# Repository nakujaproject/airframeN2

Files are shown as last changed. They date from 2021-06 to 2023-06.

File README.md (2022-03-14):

# AirframeN2

This is the repository for airframe sub-group relating to N1 rocket.






## Oboarding

For new member please checkout out onboard document [here](Onboarding/newEmployee.md)

## Research

For visitors checkout our research done by members of the airframe team [here](Research/)

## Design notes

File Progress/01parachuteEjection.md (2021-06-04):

# Parachute Ejection

This is how we will eject our parachute so that we can be able to recover our rocket after launch. There are many ways to recover the rocket mainly subdivided into pyrotechniques and non-pyrotechniques. I decided to use non-pyrotechniques as it is mainly fault tolerant and easier to make.

One mechanism in **DetMech** which was developed to automatically detach a rocket from its parachute line based on the apogee of the rocket. It is designed to assist in recovering rockets stagged by their parachutes. This method utilizes the use of a servo motor to open and close the hatch in order to eject the parachute.

Other mechanisms include :

1. Using a rubber band. The rubber band is wrapped around the body, nosecone or parachute door holding it in place until it is released.
2. Solenoid. The solenoid is used to activate thee recovery system via on board electronics usually in form of a pulse or a discharge from a capacitor. The solenoid activates a pin similary to the servo motor.
3. Mechanical armature. This involves using mechanical levers, strings and the likes.
4. Pyrotechnic. This is using a pyrotechnic charge whihc is ignited, or a wire is heated to activate the recovery system

One of the best methods is using mechanical systems since their failure rate is low. I chose servo motor as it averagely performs better in terms of cost and mode of design. The servo is an electromechanical system thus utilizing both the mechanical and electrical aspects.

## How it works

Ther mechanism is based on a simple clamp that holds the latch on to the nose cone. At the appropriate time, after maximum height has been reached with a specified delay, the clamp is moved which releases the parachute. By attaching the latch, nose cone and payload chamber to the parachute you will have a better chances in recovering the whole rocket.

The clamp is made up of a micro servo arm which is made of plastics. The latch on the other hand is made up of tough PLA material used in 3D printing the whole rocket. There can be large lateral force on the clamp during parachute opening. Aerodynamically, it has a low profile.

The bottom plate, payload chamber, which houses the electronics, is attached to the nose cone with screws rather than being glued due to large forces involved. The main parachute line should be fitted with a shock cord to reduce the stress on the clamp.

There is a little groove is to prevent the latch from moving side to side. This mechanism is contolled by the flight computer. This gives the rocket crew a chance t retrieve the rocket easily.

## More info

Using a micro servo to eject the parachute as well as detach it, will save on weight and complexity. The dual purpose mode of a single servo would be based on Christian Thomsen's RC dual chute release mechanism.
The servo could be controlled externally by a remote control. Allowing the rocketeer to release the rocket when appropriate.
A variation on the mechanism could make it completely internal to the rocket body reducing drag.
Another alternative is to replace the servo motor with a water soluble paper or plastic (such as Polyvinyl alcohol). This could be wound around the clamp to hold it down, and when it rains or humidity in the air would cause it to dissolve and release the mechanism.

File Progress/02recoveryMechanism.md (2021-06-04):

# Recovery mechanism

This is the actual deployment of the recovery mechanism in slowing down the rocket. This also includes opening latches to push out parachutes.

Some examples of the recovery mechanisms are:

1. Parachutes. This is the most effective method of recovery system.
2. Side deployment. The parachute is ejected on the outside of the rocket using some kind of spring mechanism
3. Inline deployment. The parachute is ejected along the axis of the rocket.
4. Streamer. It is deployment same as the parachute.
5. Wings, glider. This is commonly ised as passive control.
6. Changing CG, This involves changing the weight of the rocket in order to shift stability.
7. Changing CP, centre of pressure in order to move air surfaces to change the flight's stability.
8. Balloon. A balloon can be inflated from an internally stored pressure chamber in order to increase the rocket's drag.

For N1 rocket we choose the parachute system. This is too slow the rocket to an acceptable descent rate to ensure survival of the avionics. There is usually a backup system e.g deploying to parachutes or using two different methods.

A parachutre is basically a flexible device whose function is to produce drag. It slows down the rocket to a decent speed.

Dual deploy means there is a primary and secondary parachute to reduce the impact. The first is generally stronger to overcome large velocities and stabilize the rocket. The second one is attached to teh first one via a tow-line and is used to reduce drift away from launch site.

Shock cord, rubber band, is used to as a gravity coupler. This is to store kinetic energy before opening up the parachute.

Main canopy is attached to the towline to provide soft landing

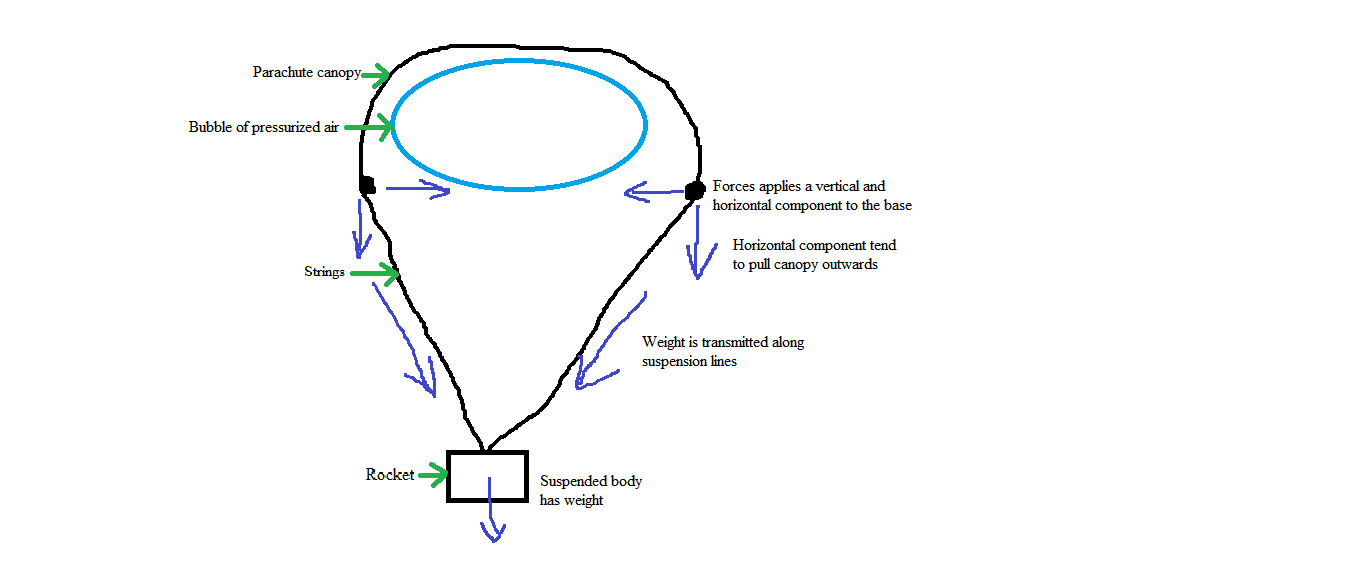
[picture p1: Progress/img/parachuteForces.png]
Parachute Forces


From the diagram above we can clearly see, according to Newton, the addition of more drag (an adverse force) results in a lower acceleration.

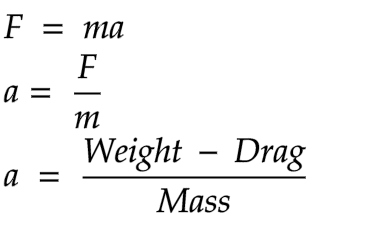
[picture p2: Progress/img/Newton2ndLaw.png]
Newton Second Law


Whether the body decelerates (negative acceleration) or not depends on the velocity and altitude of the parachute deployed.

If the body has high velocity at parachute ejection, the drag may be greater than weight.  In this case the body will decelerate. If the body has low velocity at parachute ejection, the drag may be lower than weight.  In this case the body will accelerate.

Velocity changes so as the drag. At equilibrium point the drag is equal to the weight.

If drag starts off lower than weight, acceleration will be positive. This increases velocity and drag. Drag will eventually equal weight and acceleration become zero.

When velocity isn't changing it has reached terminal velocity and it will descend at a constant velocity.

For terminal velocity drag = weight.

The parachute design process needs:

- desired shape
- weight
- drag coefficient
- determine impact velocity
- canopy area

### Desired shape

We will look at three main designs:

1. Cross

    - Easy to build

    - Lower coefficient of drag, (0.70)

    - More stable

2. Square

    - Easiest to build

    - Moderate coefficient of drag, 0.73

    - Less stable

3. Circular

    - Difficult to build

    - Higher coefficient of drag, 0.78

    - The Least stable

### Weight

At terminal velocity, drag should be equal to weight, 9.8067 N

### Drag coefficient

The drag coefficient itself depends on the Reynolds number Re. For small enough Reynolds number (of the order of few thousands or smaller) the dependence is mild and the drag coefficient is approximately constant.

### Determine impact velocity

### Canopy area

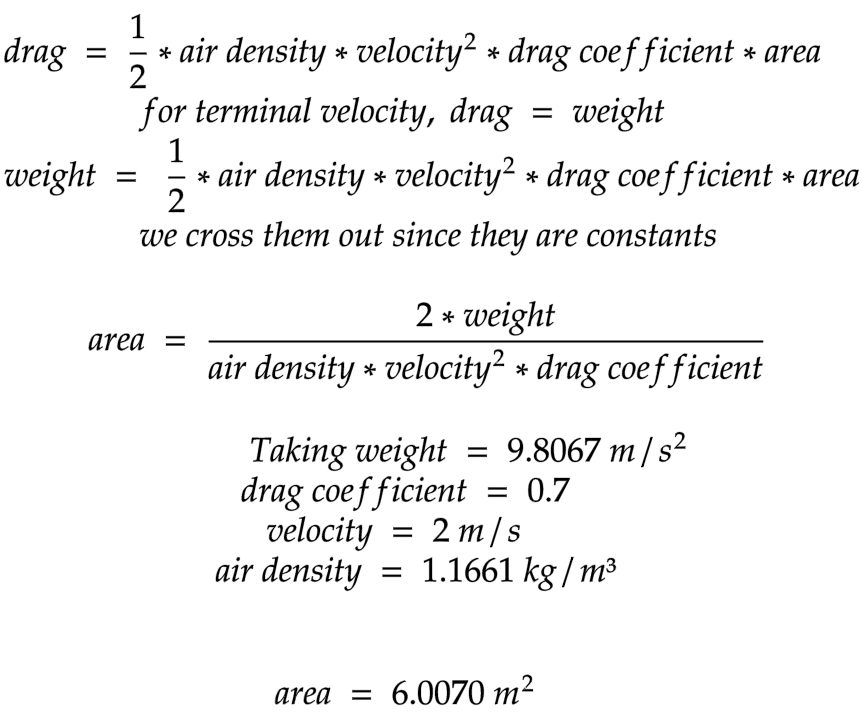
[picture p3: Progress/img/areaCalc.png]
Area calculation


Hints:

1. Get atmospheric temperature of where I am testing, [Juja](https://www.accuweather.com/en/ke/juja/828638/hourly-weather-forecast/828638)
2. Calculate the air density of where you are testing, [Juja](https://www.omnicalculator.com/physics/air-density?c=KES&v=P:1013!hPa,Temp:28!C,aaa:1.000000000000000,T:11!C)
3. Check if our area provides the drag equal to weight, [here](https://www.omnicalculator.com/physics?c=USD&v=Cd:0.7,u:2!ms,rho:1.1661!kgm3,A:6.00702!m2)

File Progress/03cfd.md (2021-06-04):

# CFD

Computational fluid dynamics (CFD) is a branch of fluid mechanics that uses numerical analysis and data structures to analyze and solve problems that involve fluid flows.

## Methodology

Some basic procedures during preprocessing are:

- The geometry and physical bounds of the problem are defined using computer aided design (CAD). From there, data is processed and the fluid volume is extracted.
- The volume occupied by the fluid is divided into discrete cells. The volume may be uniform or non-uniform or structured or unstructured.
- Physical modeling is defined, the equations of fluid motion + enthalpy + radiation + species conservation.
- Boundary conditions are defined. This involves specifying the fluid behaviour and properties at all bounding surfaces of the fluid domain. For transient problems, the initial conditions are also defined.
- The simulation is started and the equations are solved iteratively as a steady-state or transient.
- Finally, a postprocessor is used for the analysis and visualization of the resulting solution.

### Definitions

The term **compressible** refers to the relationship between density and pressure. If a flow is compressible, changes in fluid pressure affect its density and vice versa. For compressible flow, particularly supersonic flows, downstream pressure cannot affect anything upstream and the pressure equation is hyperbolic, requiring only upstream boundary conditions.

**Laminar flow** is characterized by smooth, steady fluid motion.

**Turbulent flow** is fluctuating and agitated motion. The measure of whether a flow is laminar or turbulent is the speed of the fluid. Laminar flow is typically much slower than turbulent flow. The dimensionless number which is used to classify a flow as either laminar or turbulent is the Reynolds number defined as:

Reynolds number

Where **rho** is the density, **V** is the velocity and **meu** is the viscosity. For Reynolds numbers greater than ~2500, the flow exhibits turbulent flow phenomena. Most engineering flows are turbulent.

The three-dimensional time-dependent continuity, Navier-Stokes and energy equations apply to laminar as well as turbulent flow. However, due to the infinite number of time and length scales inherent in turbulent flows, the solution of these equations require a huge number of finite elements even for a simple geometry as well as nearly infinitesimally small-time-steps. For most practical applications, it is unreasonable to model the flow in this manner.

To circumvent the need for such immense computer resources, the governing pdes are averaged over the scales present. There are several choices of scale types available for averaging. Autodesk Simulation CFD solves the time-averaged governing equations.

The time-averaged equations are obtained by assuming that the dependent variables can be represented as a superposition of a mean value and a fluctuating value, where the fluctuation is about the mean. For example, the x-velocity component can be written as:

Flactuation value

Where **U** is the mean velocity and **u'** is the fluctuation about that mean. This representation is substituted into the governing equations and the equations themselves are averaged over time.

#### Continuity Equation

Continuity Equation

**Wind tunnels** are large tubes with air blowing through them which are used to replicate the interaction between air and an object flying through the air or moving along the ground. Researchers use wind tunnels to learn more about how an aircraft will fly. The wind tunnel moves air around an object, making it seem as if the object is flying.

### Pressure measurements

Pressure across the surfaces of the model can be measured if the model includes pressure taps. This can be useful for pressure-dominated phenomena, but this only accounts for normal forces on the body.

### Flow visualizations

Because air is transparent it is difficult to directly observe the air movement itself. Instead, multiple methods of both quantitative and qualitative flow visualization methods have been developed for testing in a wind tunnel.

### Physics of fluid

Fluid is liquid and gas. For example, water and air. Fluid has many important properties, such as velocity, pressure, temperature, density and viscosity.
The density (1) of a fluid is its mass per unit volume. If the density of fluid is constant (or the change is very small), we call the fluid is incompressible fluid. If the density of fluid is not constant, we call the fluid is compressible fluid. Normally, we can treat water and air as incompressible fluid. If the fluid is incompressible, we can simplify the equations for this type of fluid.

Density

The viscosity (2) is an internal property of a fluid that offers resistance to flow. For example, to stir water is much easier than to stir honey because the viscosity of water is much smaller than honey

Viscosity

## The Process

### First open up Fusion 360

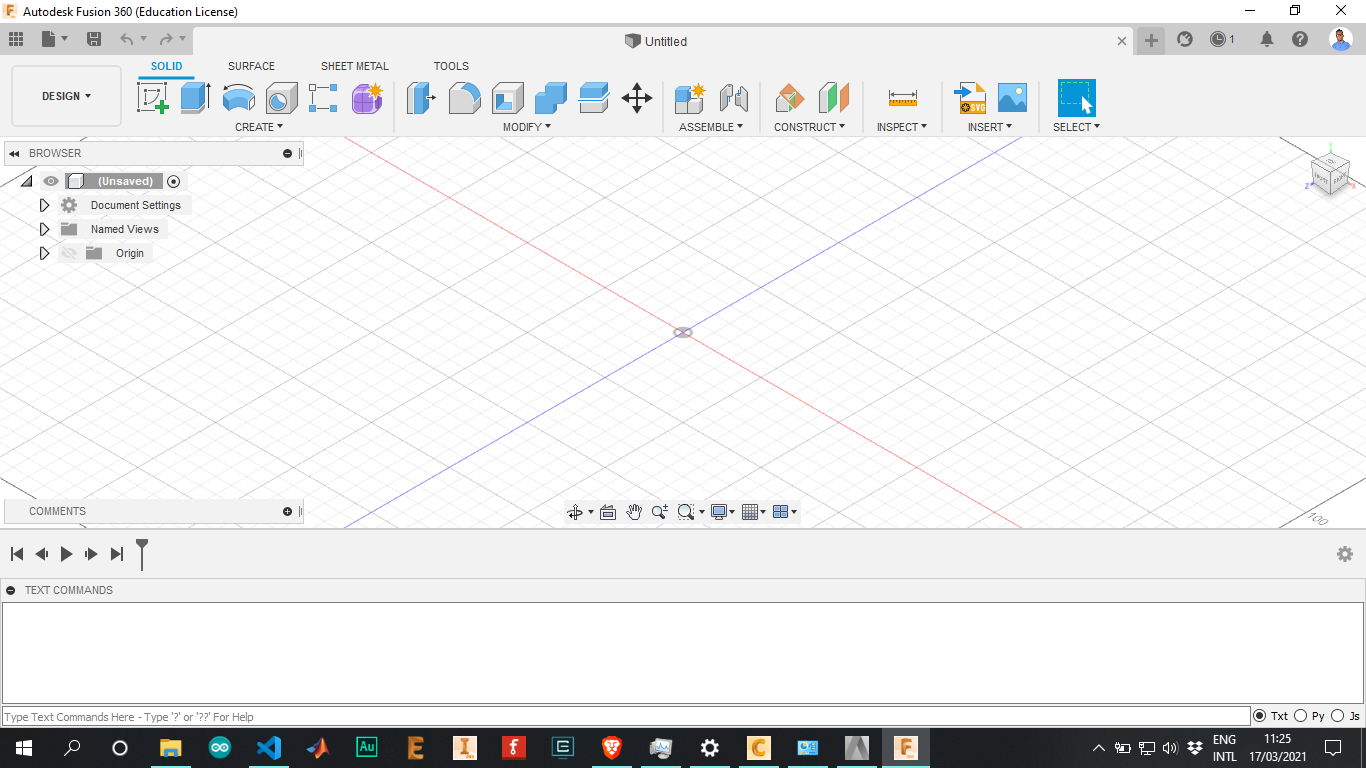
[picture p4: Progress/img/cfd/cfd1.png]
[](img/cfd/cfd1.png)

Load the assembly model

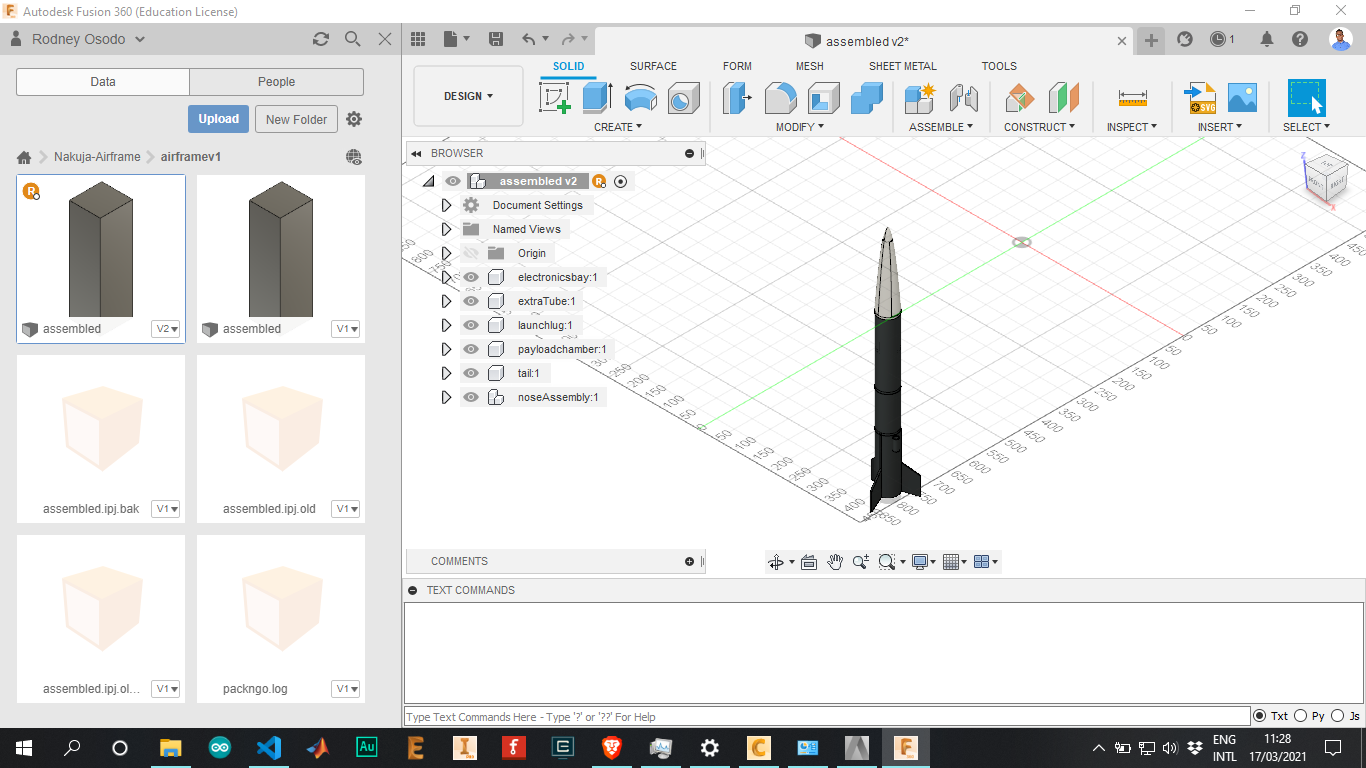
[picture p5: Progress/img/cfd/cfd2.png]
[](img/cfd/cfd2.png)

Create a wind tunnel around the model 

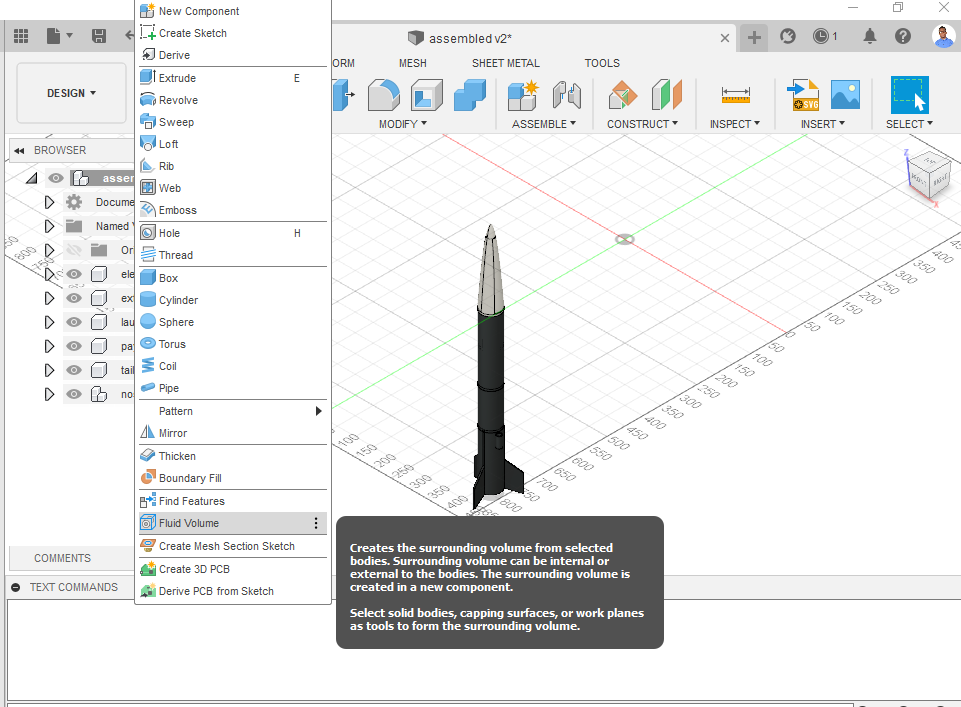
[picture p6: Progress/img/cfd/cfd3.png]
[](img/cfd/cfd3.png)

Pad the model with spacing of your choice, 50mm all around

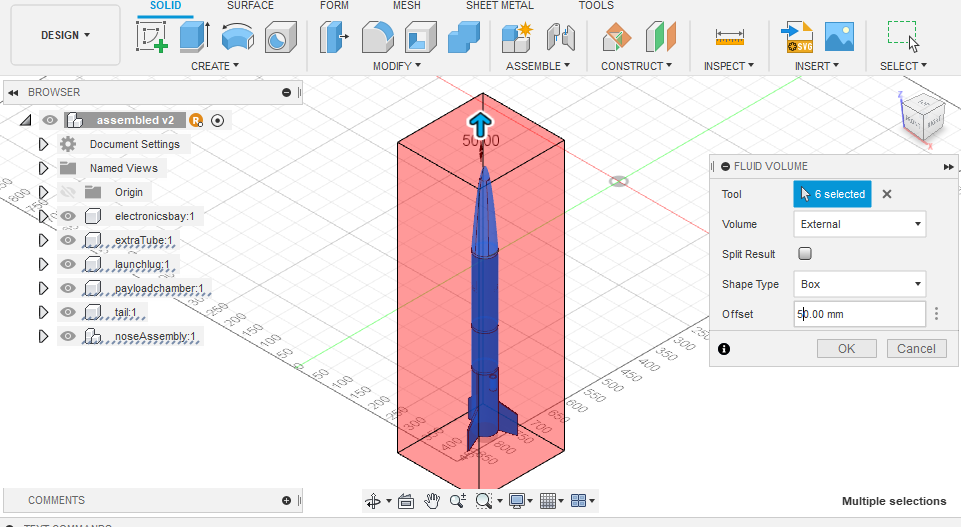
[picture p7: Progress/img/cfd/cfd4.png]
[](img/cfd/cfd4.png)

The wind tunnel is now created

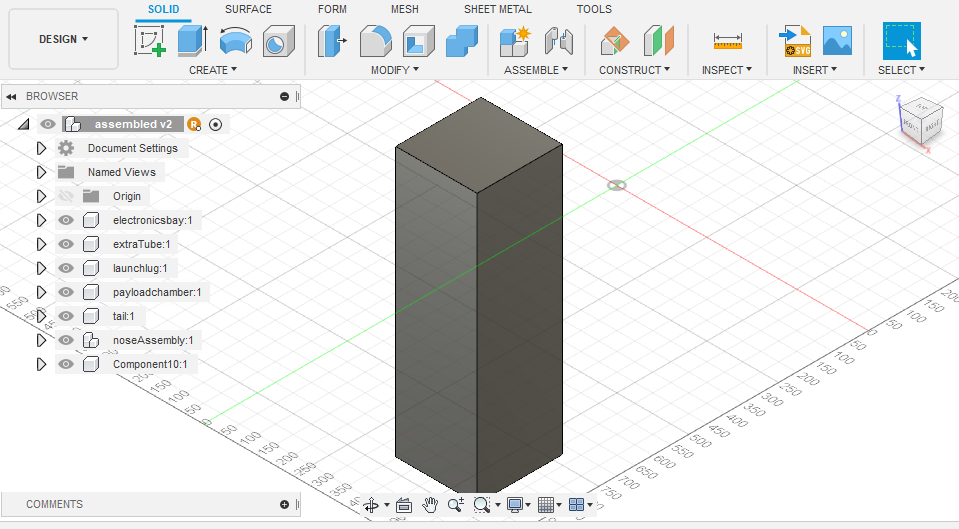
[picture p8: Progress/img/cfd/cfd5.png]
[](img/cfd/cfd5.png)

Export the file as `.step` or `.stp` file

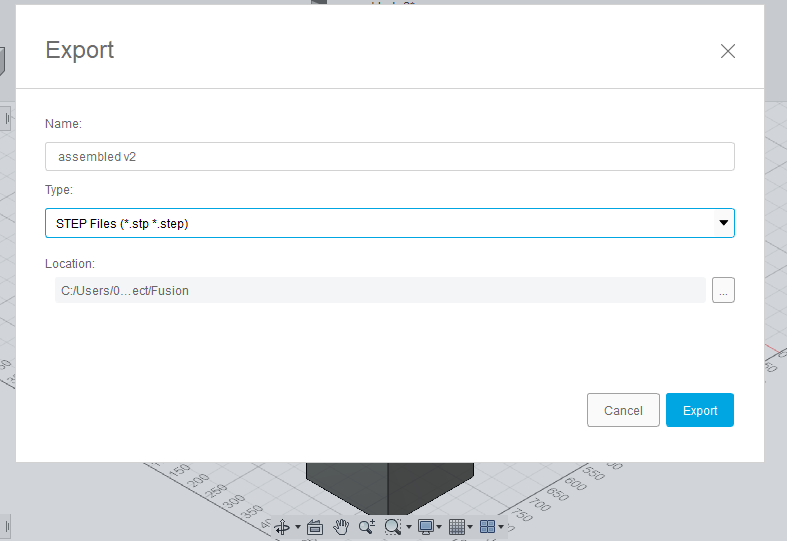
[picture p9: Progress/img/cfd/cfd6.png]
[](img/cfd/cfd6.png)

Open up Autodesk cfd/CFD

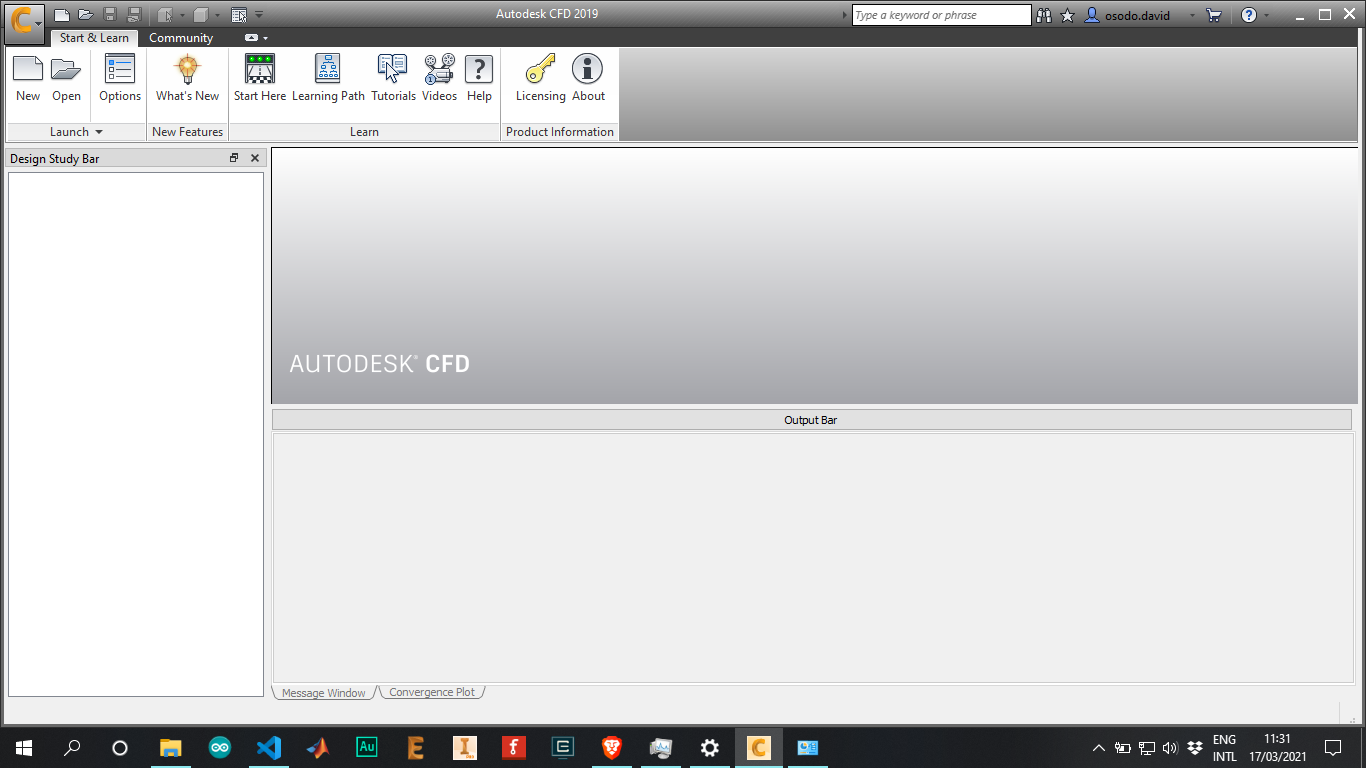
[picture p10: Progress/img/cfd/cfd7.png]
[](img/cfd/cfd7.png)

Open your `.step` or `.stp` file in CFD

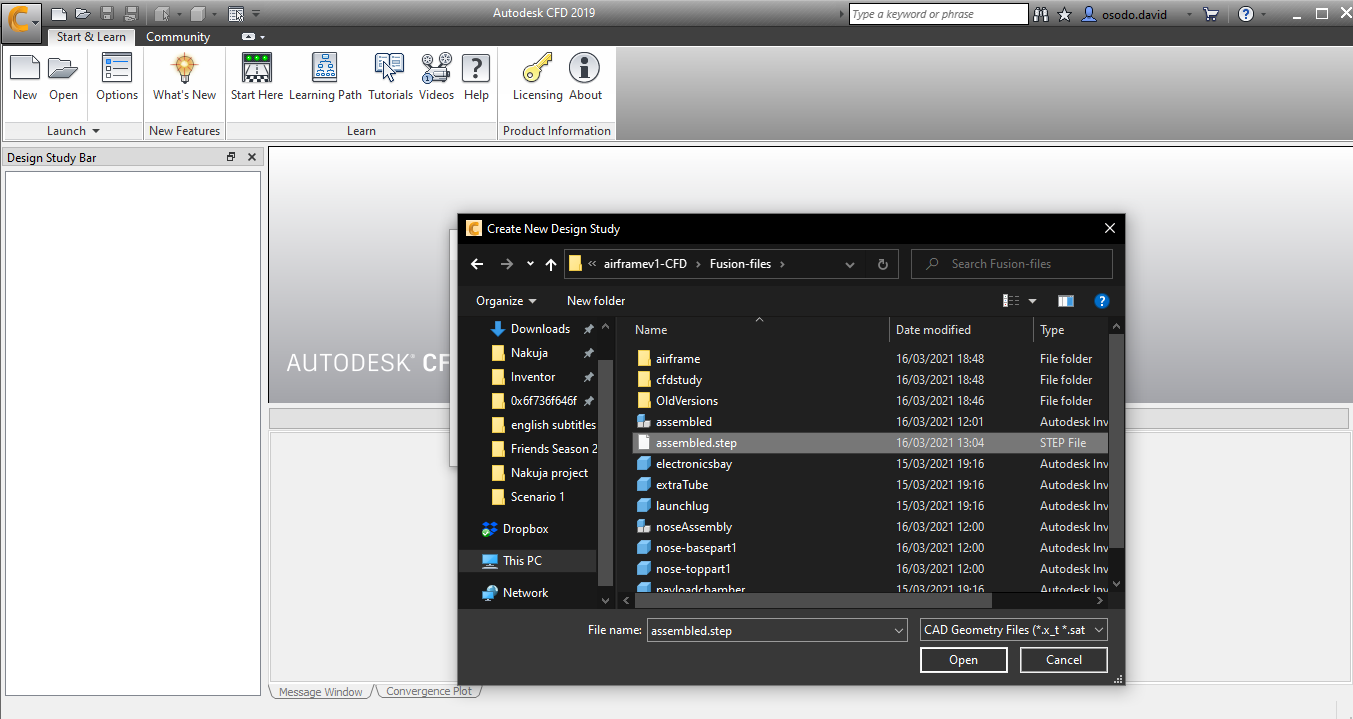
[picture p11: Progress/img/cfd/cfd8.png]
[](img/cfd/cfd8.png)

Select the parts of your model

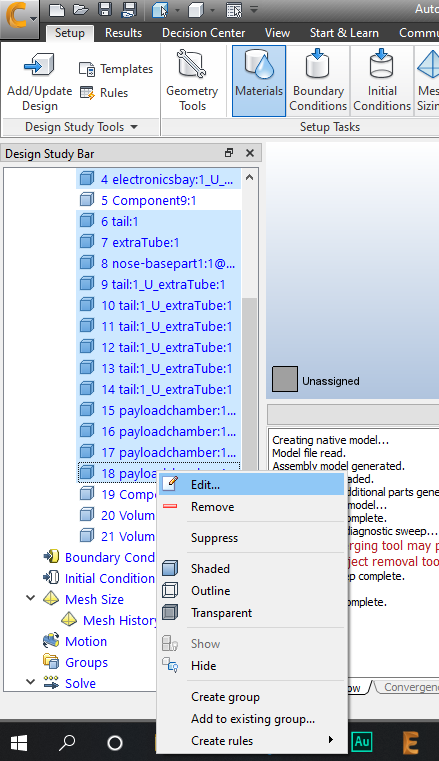
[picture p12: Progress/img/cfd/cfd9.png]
[](img/cfd/cfd9.png)

Edit the parts of the model to be solid and set them to the material of your choice

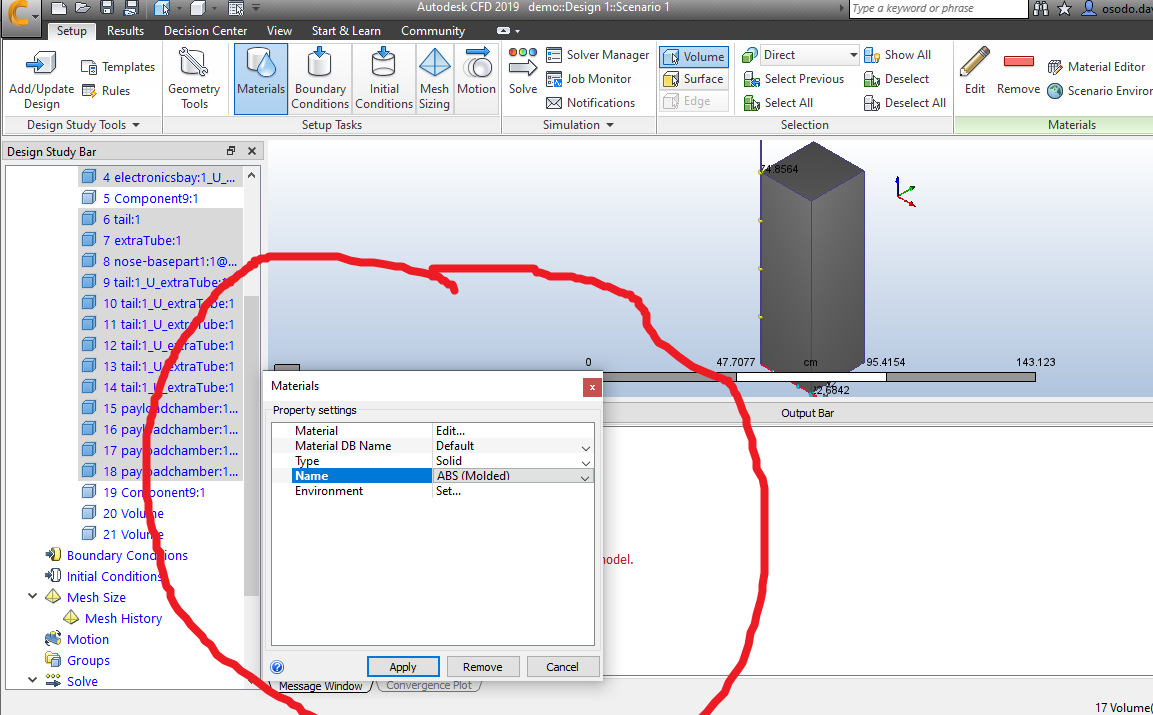
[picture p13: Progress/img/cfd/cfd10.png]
[](img/cfd/cfd10.png)

Select the components of the wind tunnel and edit them as Fluid of type air

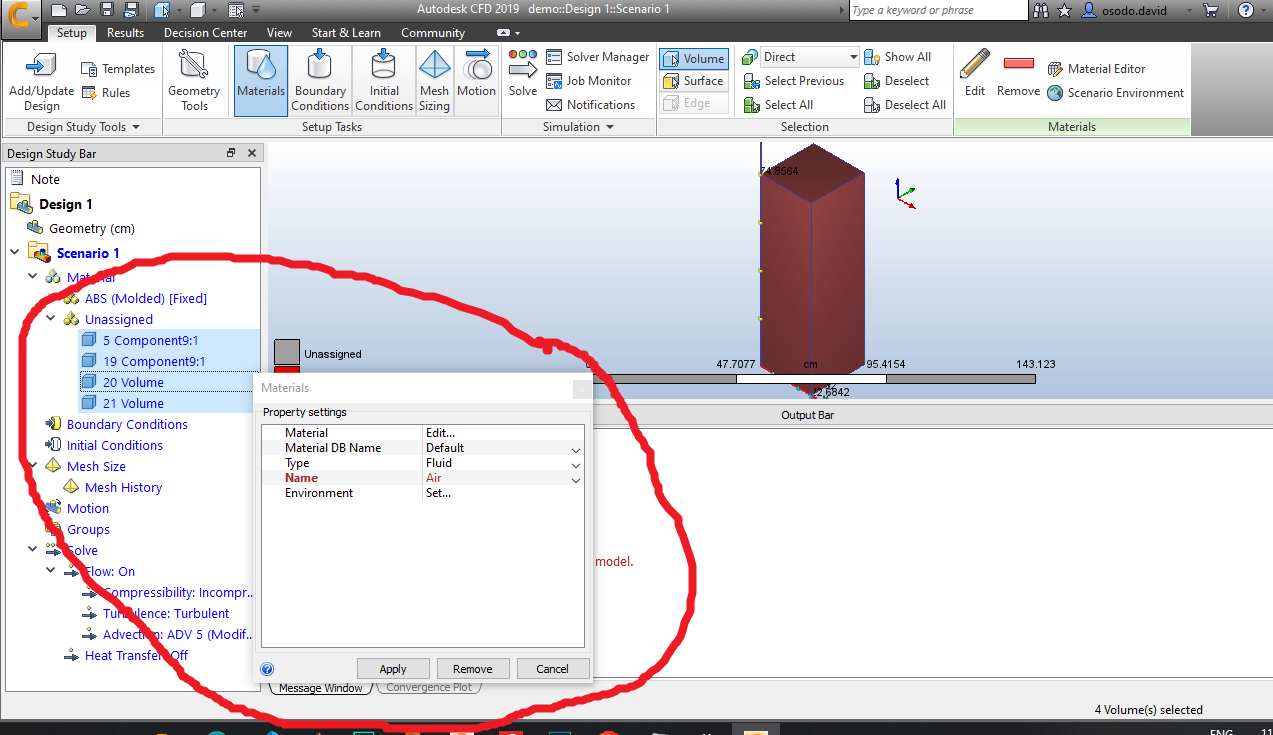
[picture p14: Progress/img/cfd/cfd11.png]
[](img/cfd/cfd11.png)

Make the wind tunnel as outline instead of solid

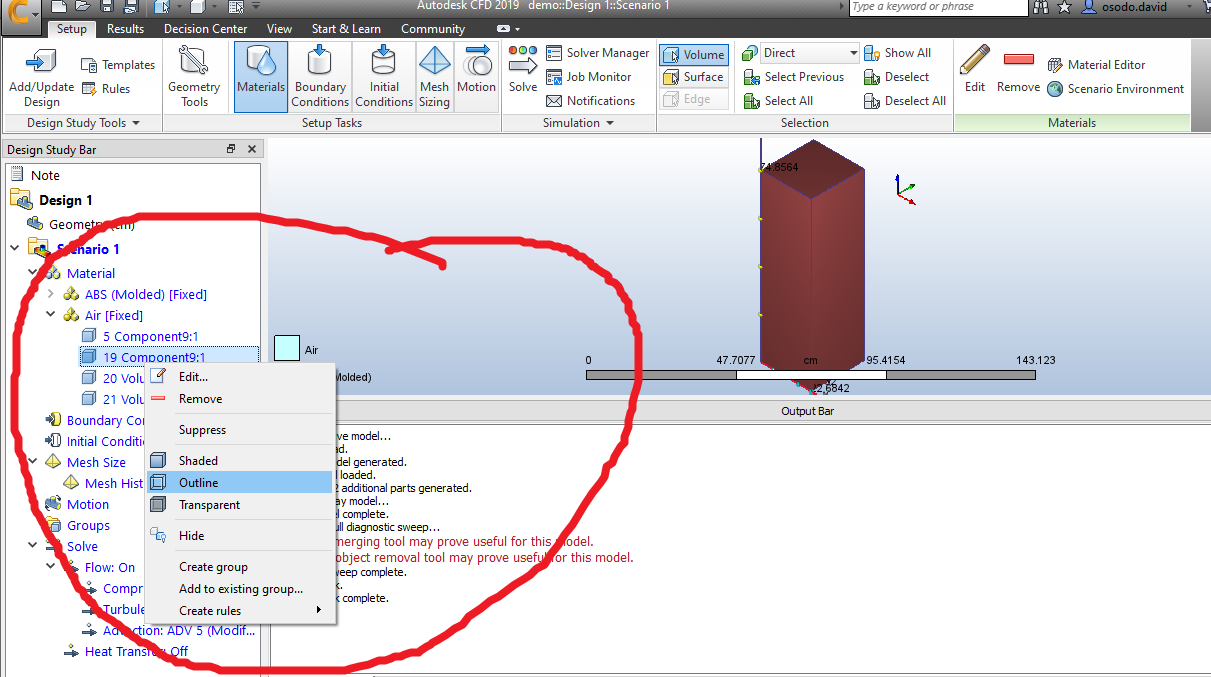
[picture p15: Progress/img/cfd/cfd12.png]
[](img/cfd/cfd12.png)

Head over to the bouddaries tab and click it

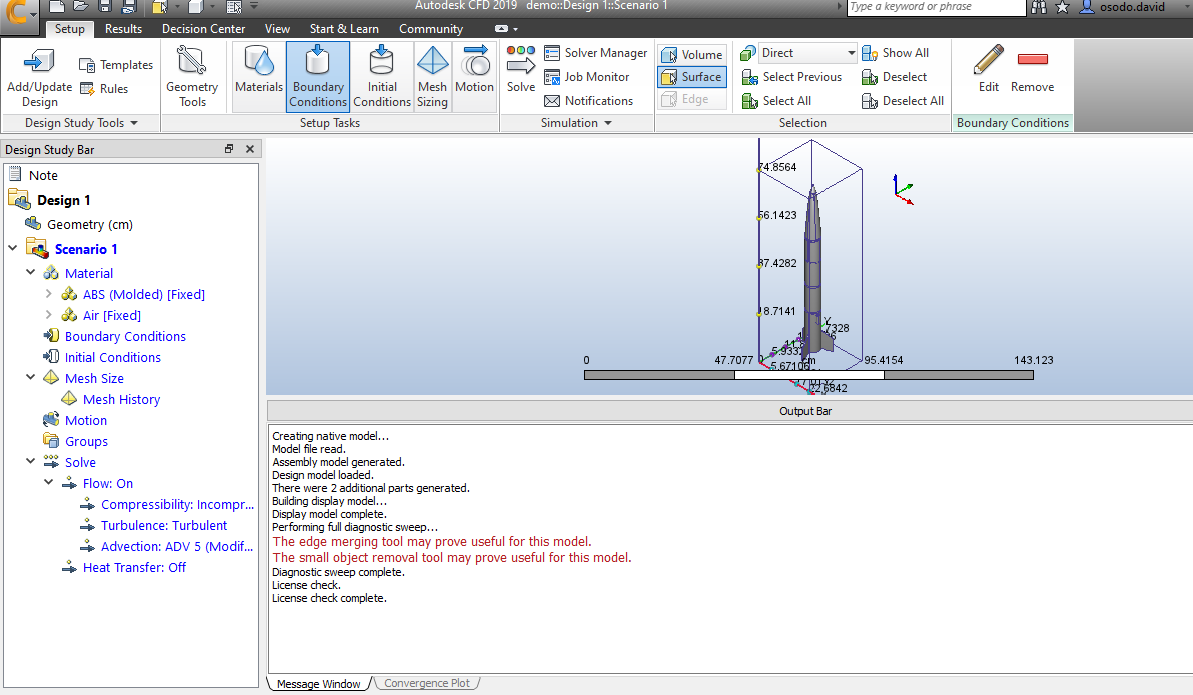
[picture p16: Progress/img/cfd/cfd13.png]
[](img/cfd/cfd13.png)

Select the rectandle at the top of the nose cone

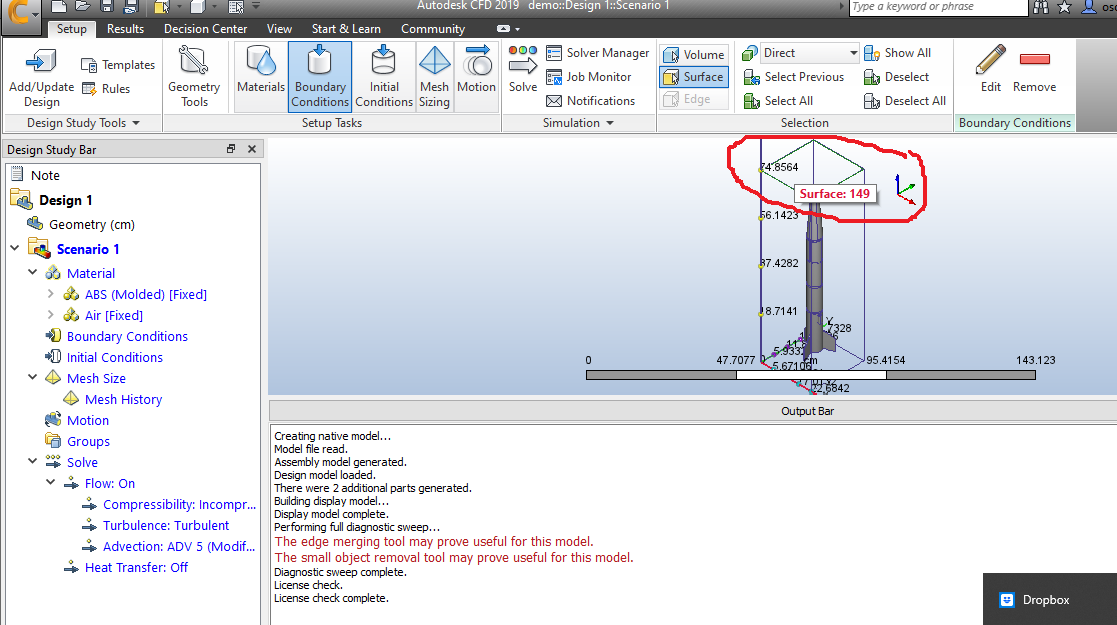
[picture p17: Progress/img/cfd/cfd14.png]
[](img/cfd/cfd14.png)

Edit is as:

- type = velocity
- unit = m/s
- time = steady state
- method = normal
- Diecrion = reverse normal
- Spatial variations = constant
- velocity magnitude = 30

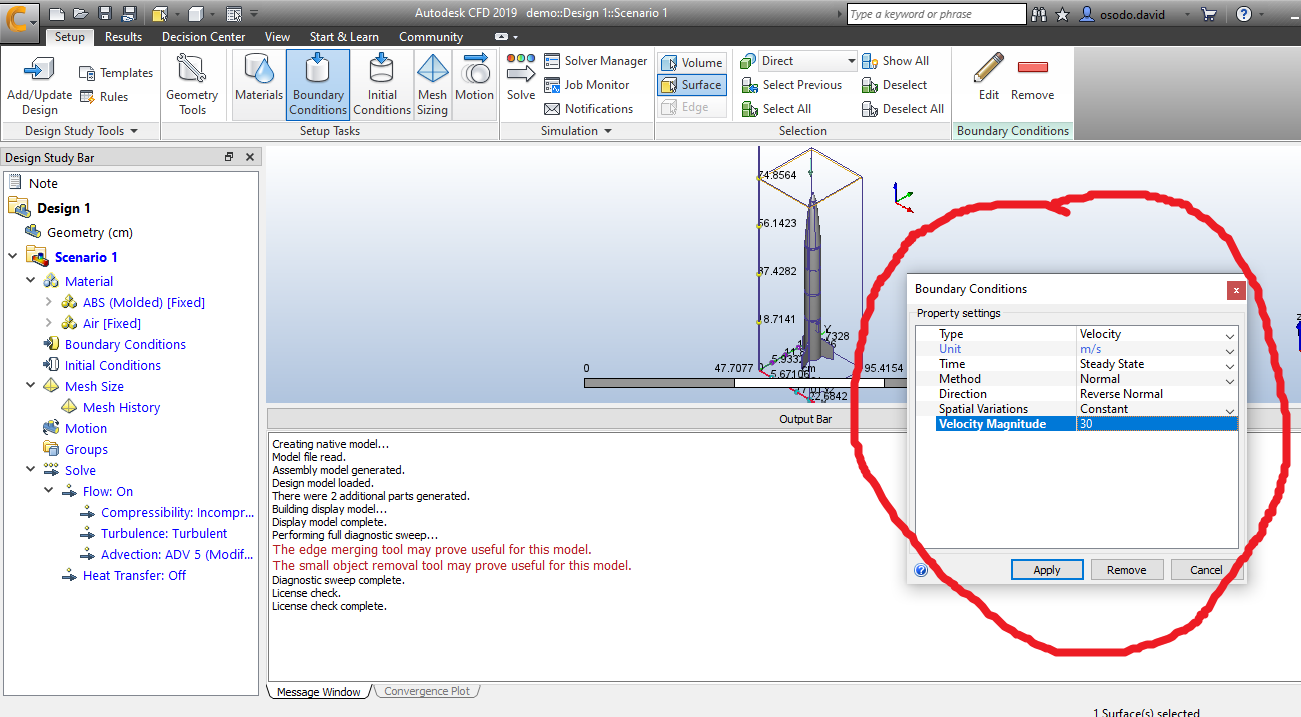
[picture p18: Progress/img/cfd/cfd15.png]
[](img/cfd/cfd15.png)

Select the rectangle as the base of the tail and edit it as:

- type = pressure
- unit = pa
- time = steady state
- pressure = 0
- Gage / Absolute = gage
- Static / Total = static

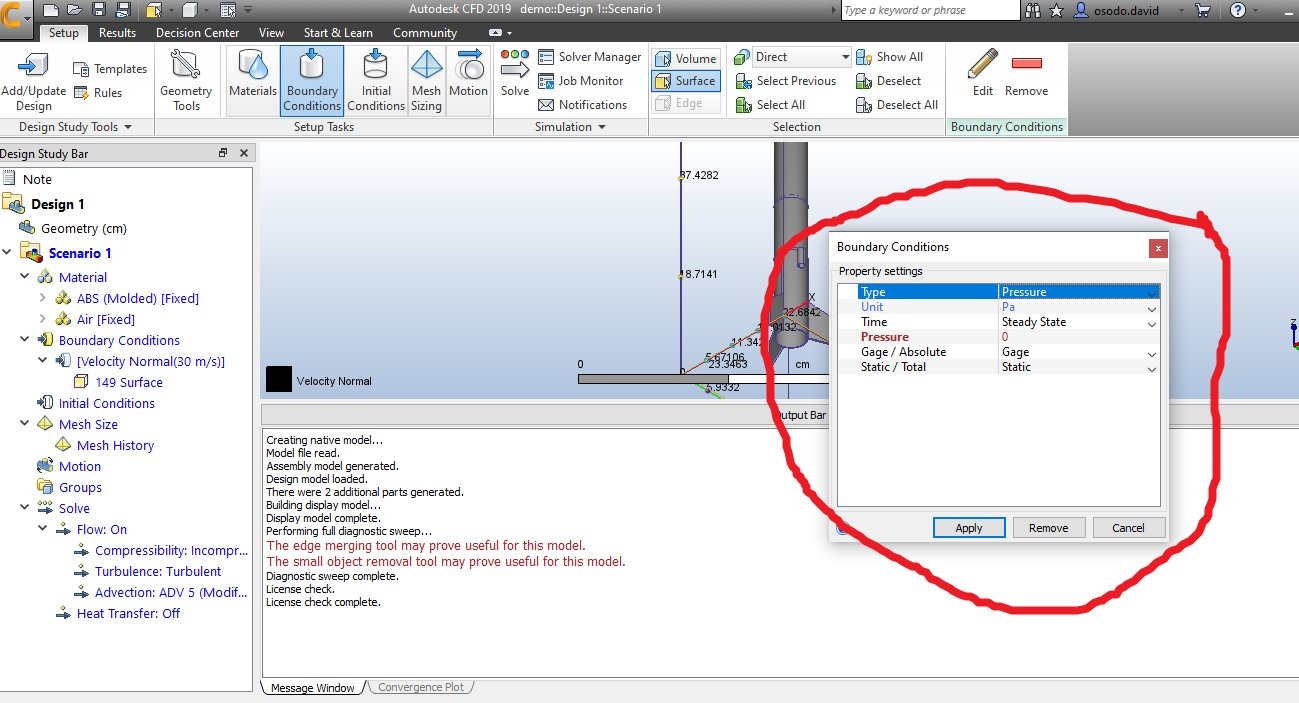
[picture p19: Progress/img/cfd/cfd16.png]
[](img/cfd/cfd16.png)

Click on the solve tab and solve

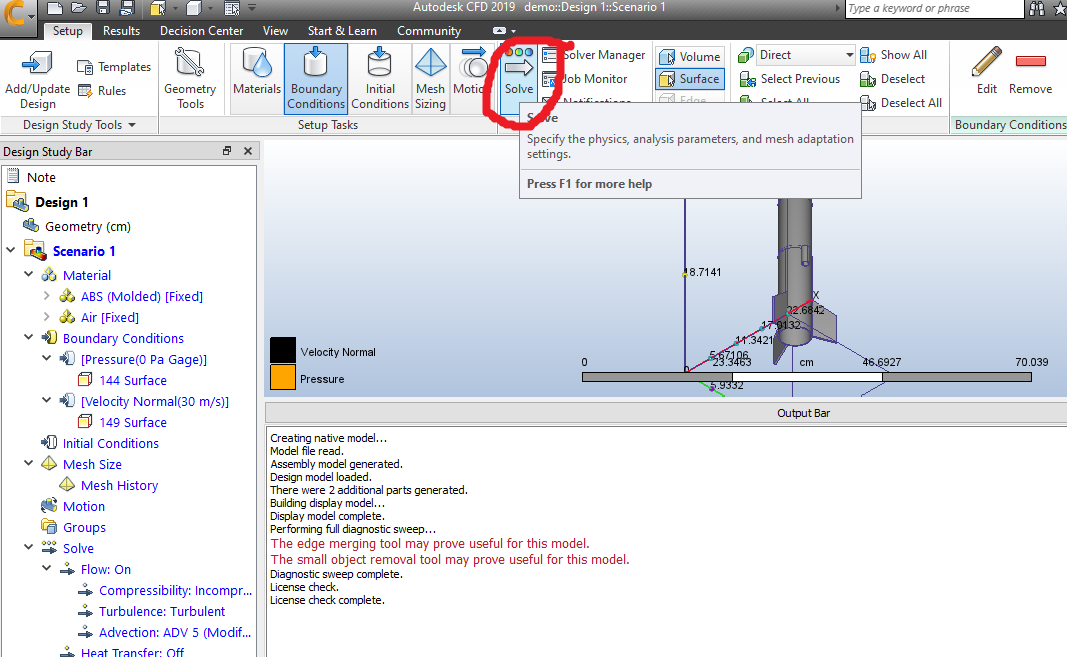
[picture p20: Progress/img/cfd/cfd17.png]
[](img/cfd/cfd17.png)

## Results

The results validated our initial hypothesis that parabolic nose cone reduce the pressure impacted on the nose and also trapezoidal fins reduce the pressure on the sides of the fins of the nose cone

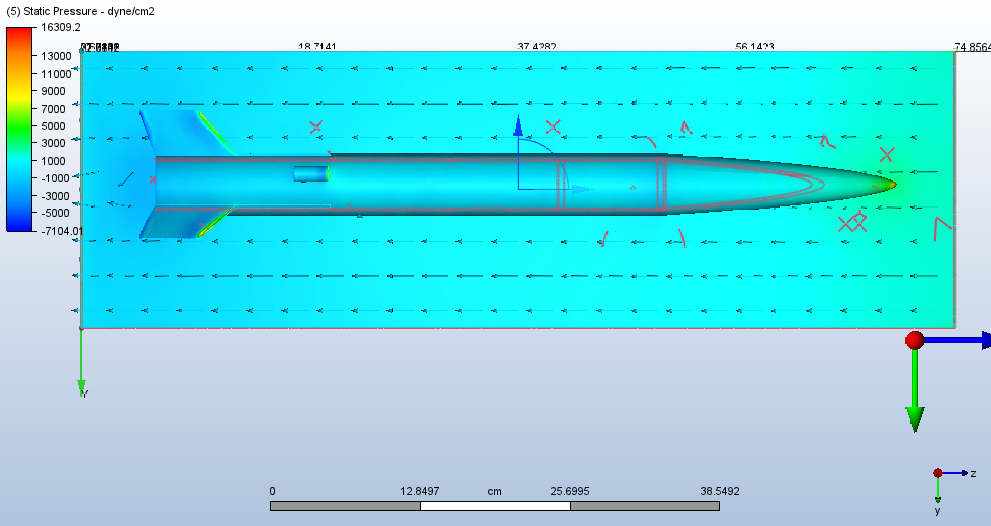
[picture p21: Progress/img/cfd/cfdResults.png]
[](img/cfd/cfdResults.png)

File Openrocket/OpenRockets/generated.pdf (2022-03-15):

## Rocket Design

H67-P

Rocket

Stages: 1

Mass (with motor): 2869 g

Stability: 2.19 cal

CG: 513 mm

CP: 644 mm

Altitude | 187 m
Flight Time | 54.1 s

Time to Apogee 7.38 s

Optimum Delay 4.45 s

Velocity off Pad 6.71 m/s

Max Velocity | 50.5 m/s
Velocity at Deployment | 3 m/s
Landing Velocity | 3.86 m/s
Motor | Avg Thrust | Burn Time | Max Thrust | Total Impulse | Thrust to Wt | Propellant Wt Size
H67 | 81.2 N | 2.46 s | 159 N | 201 Ns | 2.88:1 | 300 g | 50/100 mm

## Parts Detail

Sustainer

Nose cone | PLA

(1.3 g/cm³)

Ogive | Len: 180 mm | Mass: 93.5 g
Body | Fiberglass

(1.85 g/cm³)

Diain | 56 mm
Diaout 60 mm | Len: 668 mm | Mass: 450 g
Parachute | Ripstop nylon

(67 g/m²)

Diaout 2000 mm | Len: 90 mm | Mass: 263 g
Shroud Lines | Tubular nylon
(25 mm, 1 in)

(29 g/m)

Lines: 6 | Len: 300 mm
Shock cord | Elastic cord
(round 2 mm,
1/16 in)

(1.8 g/m)

Len: 400 mm | Mass: 20 g
Parachute block | Aluminium

(2.8 g/cm³)

Diain 30 mm
Diaout 56 mm
Len: 10 mm | Mass: 49.2 g
Flight Control | Diaout 56 mm | Mass: 250 g
Flight control block | Aluminium

(2.8 g/cm³)

Diain | 30 mm
| Diaout 56 mm
Len: 10 mm | Mass: 49.2 g
Electronics bay | PLA

(1.3 g/cm³)

Diain | 50 mm
| Diaout 56 mm
Len: 130 mm | Mass: 84.4 g
Flight computer | Diaout 50 mm | Mass: 800 g
Altimeter block | Aluminium

(2.8 g/cm³)

Diain | 30 mm
| Diaout 56 mm
Len: 10 mm | Mass: 49.2 g
Launch lug | PLA

(1.3 g/cm³)

Diain | 8 mm
| Diaout 10 mm
Len: 30 mm | Mass: 1.1 g
Trapezoidal fin set (3) | Fiberglass

(1.85 g/cm³)

| Thick: 2 mm | Mass: 46.2 g
Centering ring | PLA

(1.3 g/cm³)

Diain | 0 mm
| Diaout 56 mm
Len: 15 mm | Mass: 48 g
Centering ring | PLA

(1.3 g/cm³)

Diain | 50 mm
| Diaout 56 mm
Len: 14 mm | Mass: 9.09 g
Engine block | PLA

(1.3 g/cm³)

Diain | 20 mm
| Diaout 56 mm
Len: 20 mm | Mass: 55.9 g

## Launch lug Trapezoidal fin set

## Trapezoidal fin set

## Trapezoidal fin set

Front

in cm

cm
in

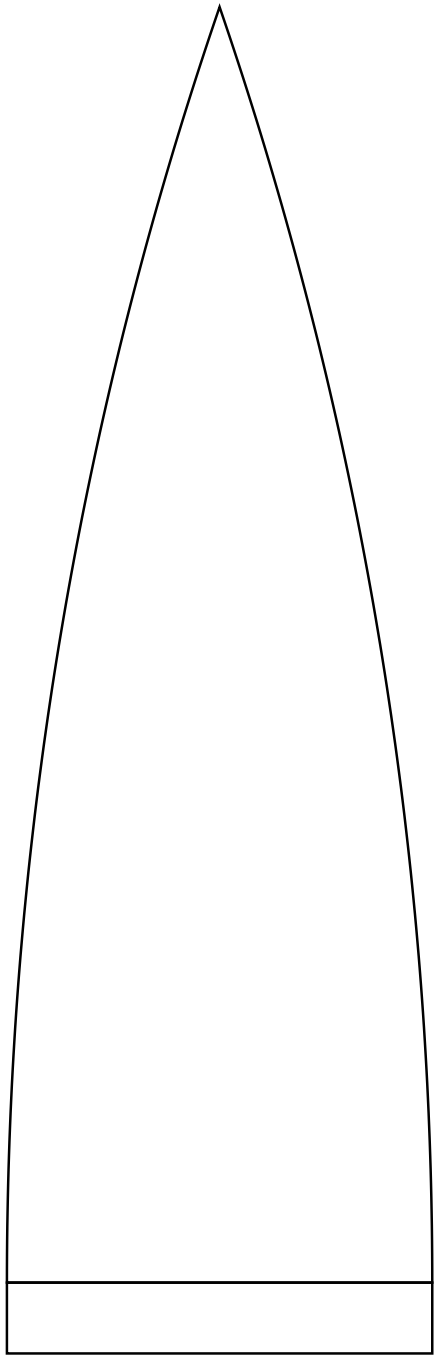
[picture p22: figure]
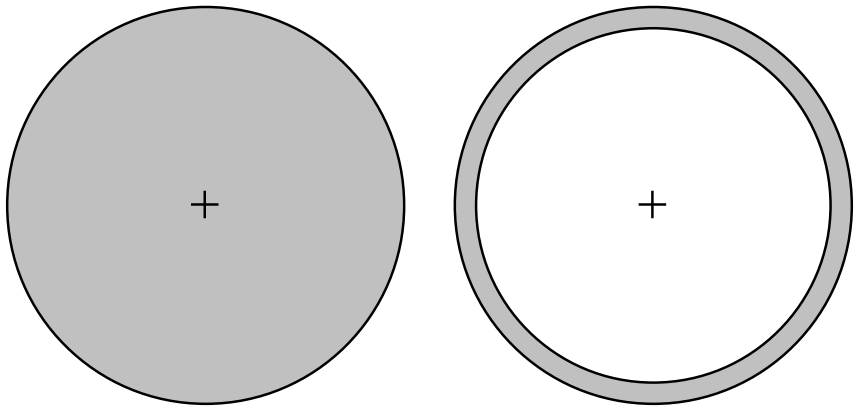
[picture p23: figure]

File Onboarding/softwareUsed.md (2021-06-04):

# Used software

## Initial Design

Currently we are using [Openrocket v15.03](https://github.com/openrocket/openrocket/releases/download/release-15.03/OpenRocket-15.03.jar)

## Computer Aided Design

Currently we are using [Inventor 2020](https://knowledge.autodesk.com/support/inventor/learn-explore/caas/CloudHelp/cloudhelp/2020/ENU/Inventor-WhatsNew/files/GUID-8126E8EE-422A-4DEF-9B14-513D87BD4122-htm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's,the%20release%20of%20Inventor%202020.&text=Inventor%202020%20delivers%3A,a%20modernized%20look%20and%20feel.)

## Analysis

For fluid analysis we are using [CFD 2019](https://knowledge.autodesk.com/support/cfd/troubleshooting/caas/downloads/content/autodesk-cfd-2019-download-and-install-help-documentation.html)

The Autodesk fusion version we are using is [Fusion 360](https://www.autodesk.com/products/fusion-360/free-trial)

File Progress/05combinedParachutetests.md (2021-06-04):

# Parachute tests

| Nose cone version | Prachute included | Explanation |
| --- | --- | ---|
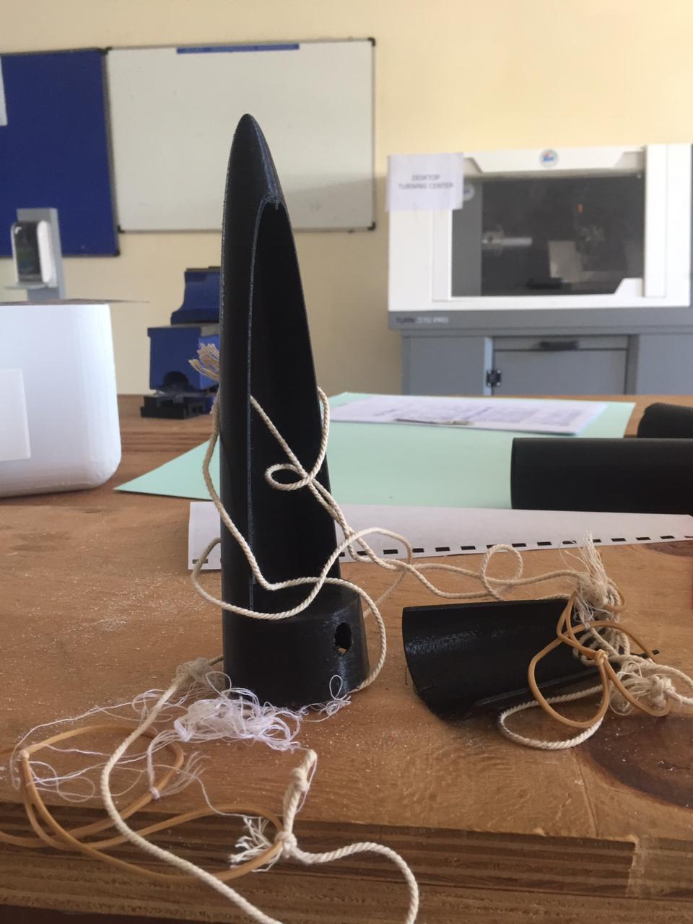
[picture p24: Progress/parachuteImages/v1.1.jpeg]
v1.1 Nose cone
 | Parachute p1 | [Read more here](parachuteTests/v1.1.md)
v2.1 Nose cone | Parachute p2 | [Read more here](parachuteTests/v2.1.md)
v3.1 Nose cone | Parachute p2 | [Read more here](parachuteTests/v3.1.md)
v3.2 Nose cone | Parachute p2 | [Read more here](parachuteTests/v3.2.md)
v4.1 Nose cone | Parachute p3 | [Read more here](parachuteTests/v4.1.md)
v5.1 Nose cone | Parachute p3 | [Read more here](parachuteTests/v4.1.md)

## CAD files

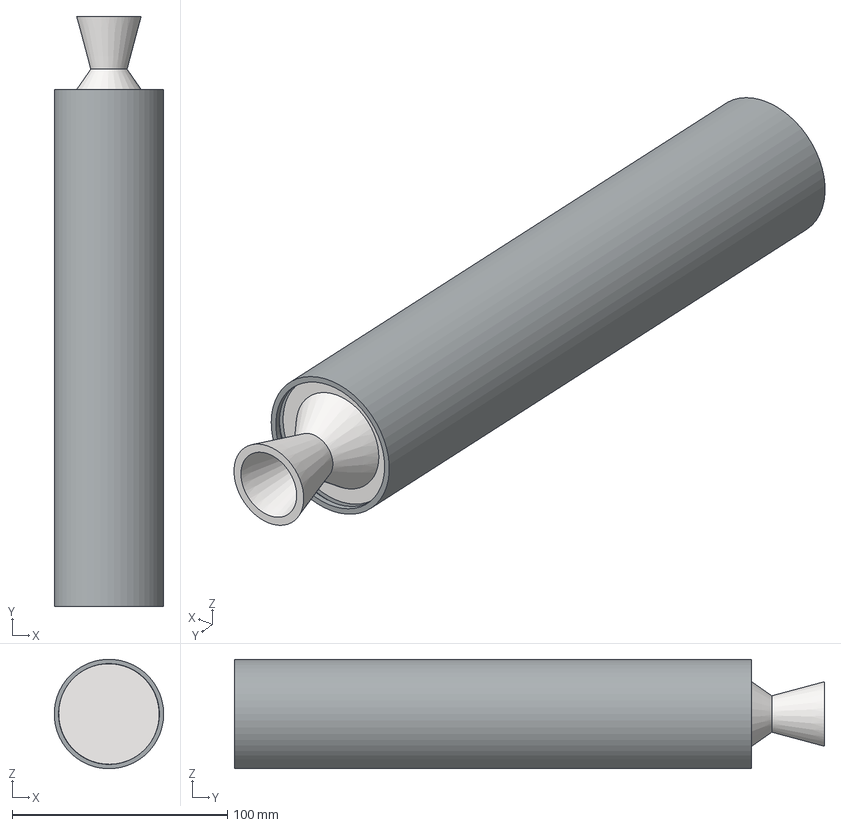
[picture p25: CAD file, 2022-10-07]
CAD/Launch/Propulsion/Assembly.stp
50.8 x 273.8 x 50.8 mm
bulkhead
casing
nozzle

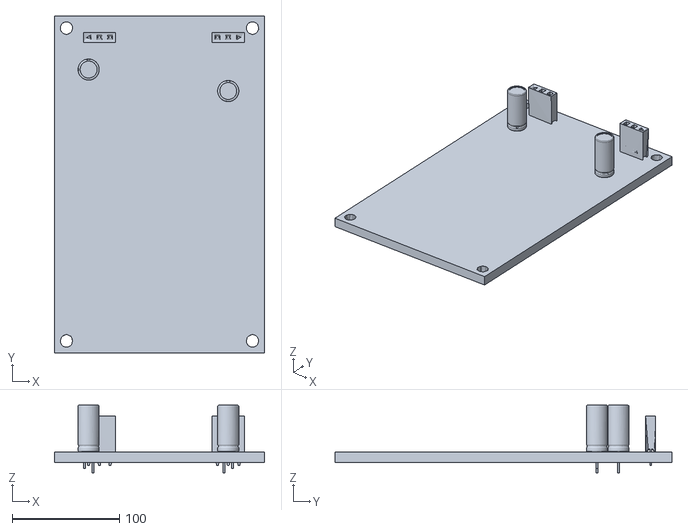
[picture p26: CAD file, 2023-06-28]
CAD/Launch/flight-control/OBJ_PCB_flight-control_2.obj
195.6 x 313.8 x 63.1

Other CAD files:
CAD/Launch/Avionics/PCB_PCB_N2-final launch PCB1_2022-10-12 (9).iam
CAD/Launch/Propulsion/Inventor files/Assembly.iam
CAD/Launch/Propulsion/Inventor files/OldVersions/bulkhead.0001.ipt
CAD/Launch/Propulsion/Inventor files/OldVersions/casing.0001.ipt
CAD/Launch/Propulsion/Inventor files/OldVersions/nozzle.0001.ipt
CAD/Launch/Propulsion/Inventor files/bulkhead.ipt
CAD/Launch/Propulsion/Inventor files/casing.ipt
CAD/Launch/Propulsion/Inventor files/nozzle.ipt
CAD/Launch/flight-control/Assembly1.iam
CAD/Launch/flight-control/OBJ_PCB_PCB_Flight control computer.ipt
CAD/Launch/flight-control/OBJ_PCB_flight-control_2.ipt
CAD/Launch/flight-control/Reaction_wheel_dr - Copy (3.3) (1).ipt
CAD/Launch/flight-control/battery holder.ipt
CAD/Launch/flight-control/case v0.ipt
CAD/Launch/flight-control/motorMotor_BLDC_2212,6T_2200KV__With_Support.ipt
CAD/N2 CAD airframe/Body Tube/body tube n-2.ipt
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

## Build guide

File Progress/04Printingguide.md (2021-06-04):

# 3D prinitng basics on `ULTIMAKER s3`

## Theory

This is from the ultimaker site.

### Layer height

It is the thickness of one printed layer in millimeters.
Thinner layer height increases the quality of the print, leading to a smoother surface and more detail model.

### Initial layer height

This is the height of the first layer of your print. The initial layer height is usually thicker than the layer height to create a stronger adhesion with the build plate.

### Line width

The width of a single printed line, which should be close to the nozzle size.

- Top surface skin line width: This line width is only available when a top surface skin is used.
- Top/bottom line width: The line width with which the top and bottom layers are printed.
- Infill line width: The line width of all infill material.

### Infill density

It is the amount of plastic used on the inside of the print. A higher infill density means that there is more plastic on the inside of your print, leading to a stronger object.

### Infill pattern

This is the pattern of the infill material.

- Strong 2D infills are used for everyday prints
- Quick 2D infills are used for quick, but weak models
- 3D infills are used to make the object equally strong in all directions
- 3D concentric infills are used for flexible materials

The following pattern options are available:

- Grid: Strong 2D infill
- Lines: Quick 2D infill
- Triangles: Strong 2D infill
- Tri-hexagon: Strong 2D infill
- Cubic: Strong 3D infill
- Cubic (subdivision): Strong 3D infill (this saves material compared to Cubic)
- Octet: Strong 3D infill
- Quarter cubic: Strong 3D infill
- Concentric: Flexible 3D infill
- Zig-zag: A grid shaped infill, printing continuously in one diagonal direction
- Cross: Flexible 3D infill
- Cross 3D: Flexible 3D infill
- Gyroid infill: Infill with increased strength for the lowest weight.

### Printing temperature

The temperature of the nozzle while printing, including the adapted extrusion rate. Each printing profile has a slightly different printing temperature to create the best print result.

### Build plate temperature

The heated bed temperature during the printing process. Each material has an ideal build plate temperature, which is set here.

### Print speed

The print speed defines the speed (in mm/s) at which the print head moves while printing. Based on this setting, Ultimaker Cura calculates the extrusion flow.

A higher print speed will lead to a shorter print time. Keep in mind that increasing the print speed means that you may have to increase the temperature as well to ensure the filament is properly melted.

### Enable cooling fans

With this setting you can enable or disable the print head fans during printing. The print head fans ensure that the material is cooled properly before the next layer is printed. For layers with a short layer time, and those with bridges/overhangs, cooling will increase the print quality.

### Fan speed

When the print head fans are enabled, you can adjust certain parameters. One of these is the fan speed – the speed at which the fans spin. A higher speed allows for better cooling and reduces oozing, but can also increase the shrinkage of the material.

### Build plate adhesion

#### Raft

A raft adds a thick grid with a roof between the model and the build plate. This can be useful when the bottom surface of a model is not completely flat or has little adhesion to the build plate. A raft ensures that the model will stick better to the build plate.

#### Brim

Brim adds a single layer flat area around the base of the model to prevent warping. The brim is connected to the model and makes the bottom surface area bigger. This increases the adhesion to the build plate and, in case of warping, the corners of the model are less likely to curl up because of the brim attached to it.

## Process

### 1. Open your model to import it inside ultimaker cura software

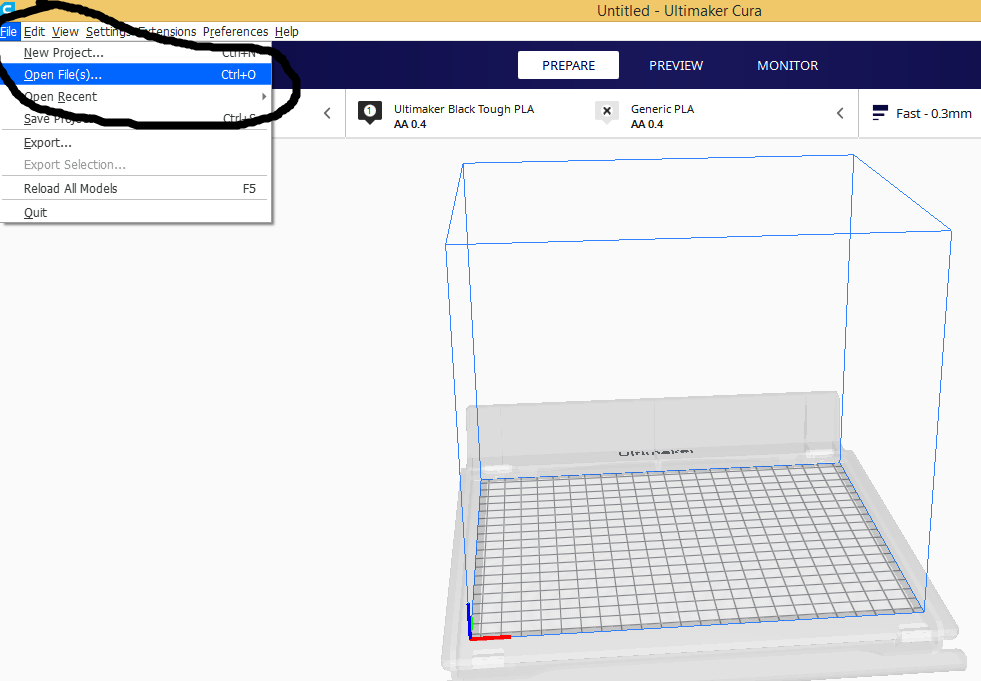
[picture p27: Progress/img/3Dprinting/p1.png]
[](img/3Dprinting/p1.png)

### 2. The model has been imported with the orientation in which you drew it

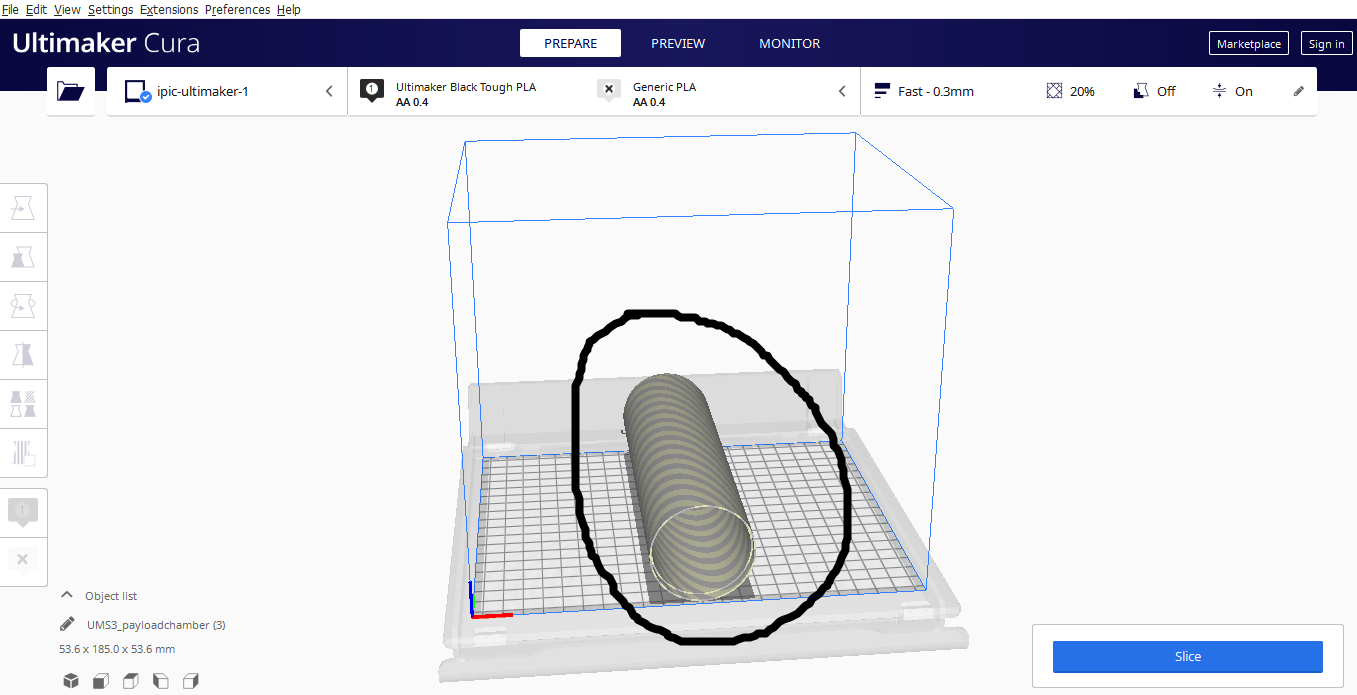
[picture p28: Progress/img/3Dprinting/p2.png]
[](img/3Dprinting/p2.png)

### 3. Change the orientation so that it lies vertically

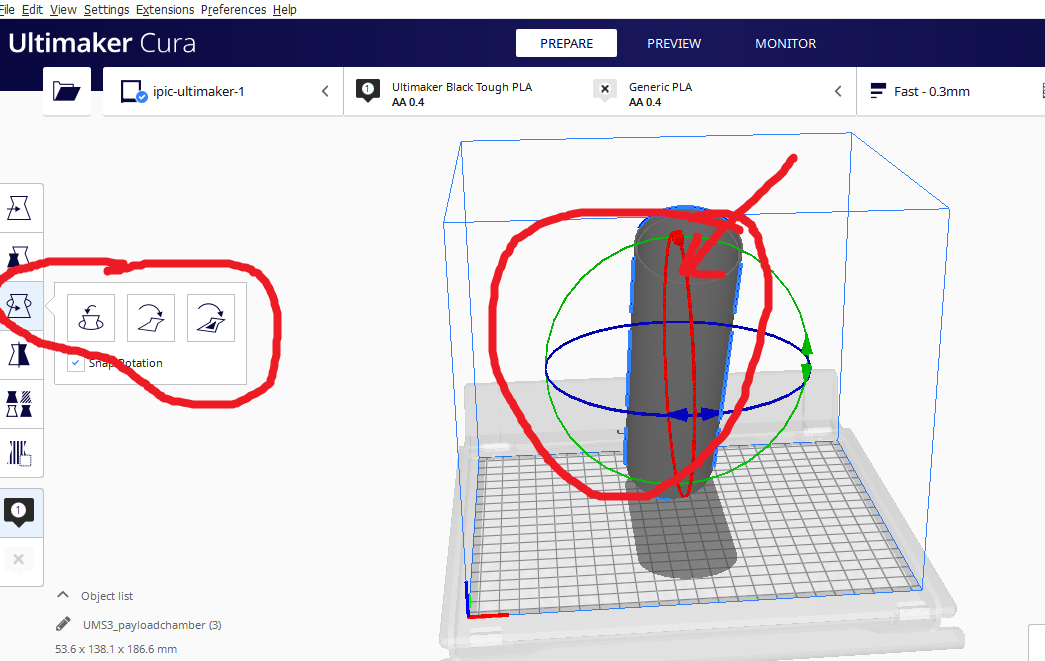
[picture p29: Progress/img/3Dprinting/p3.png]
[](img/3Dprinting/p3.png)

### 4. Click on the lay flat so that it can automatically set the base to the bed

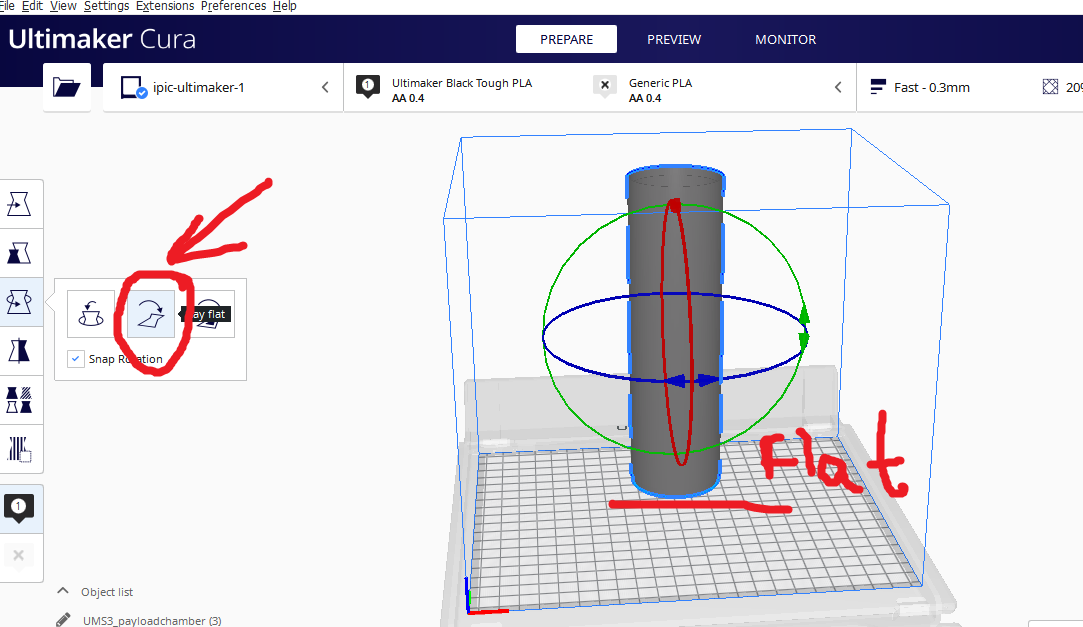
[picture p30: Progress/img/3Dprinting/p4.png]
[](img/3Dprinting/p4.png)

### 5. Center the model on the bed

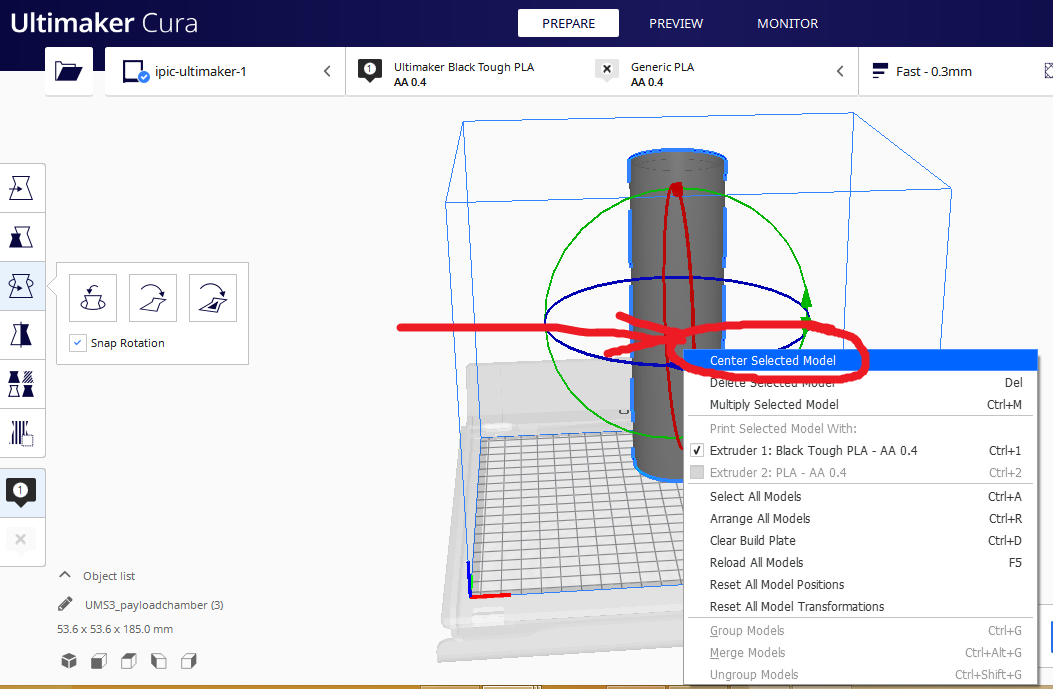
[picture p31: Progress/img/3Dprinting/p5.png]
[](img/3Dprinting/p5.png)

### 6. You can scale down the model with the height alone. Click to remove uniform scaling in order to scal e the height alone

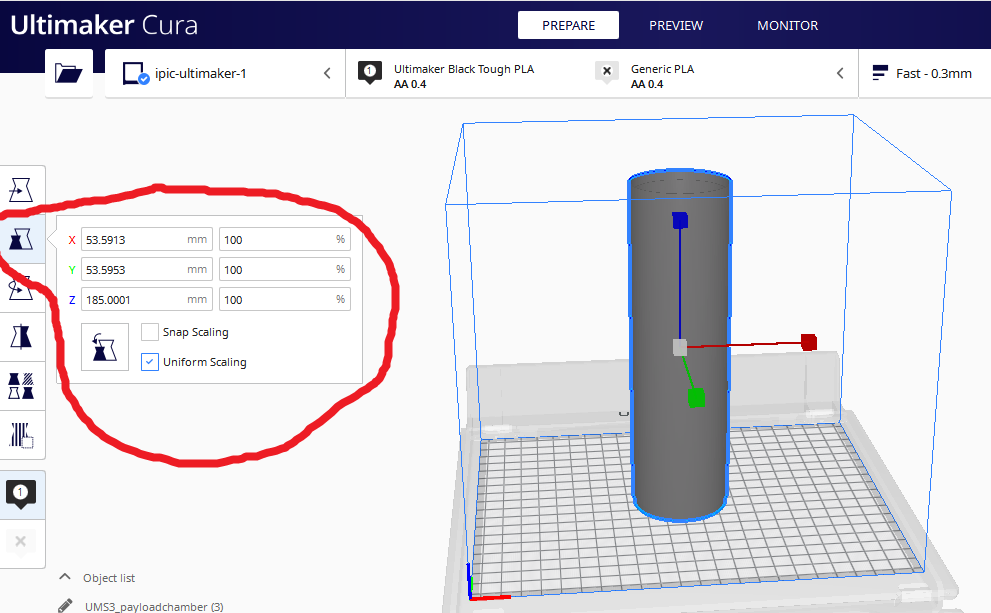
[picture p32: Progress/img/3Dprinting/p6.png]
[](img/3Dprinting/p6.png)

### 7. The model has been scaled down in terms of height

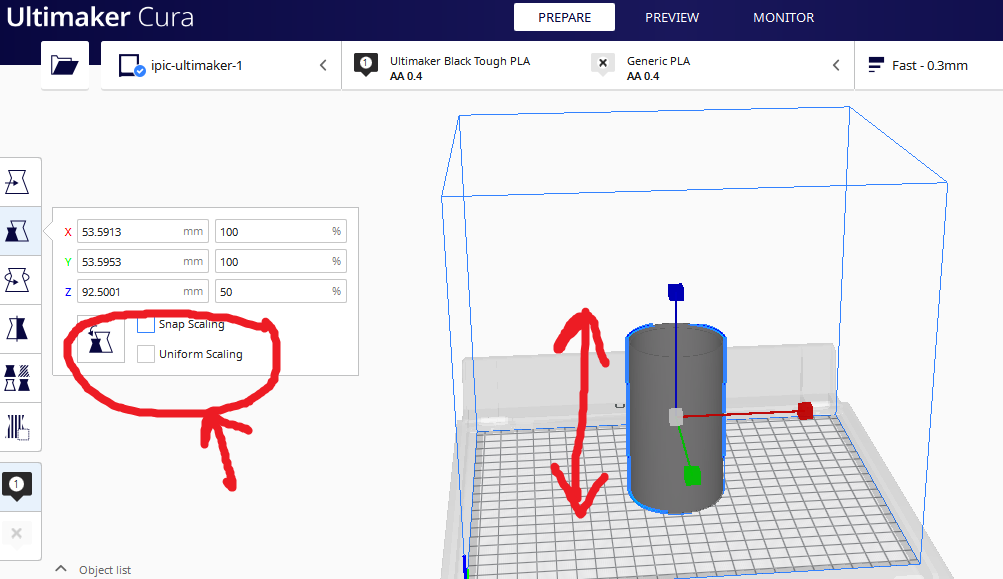
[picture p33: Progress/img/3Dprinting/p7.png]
[](img/3Dprinting/p7.png)

### 8. Click on the top right conrer in order to change the print settings

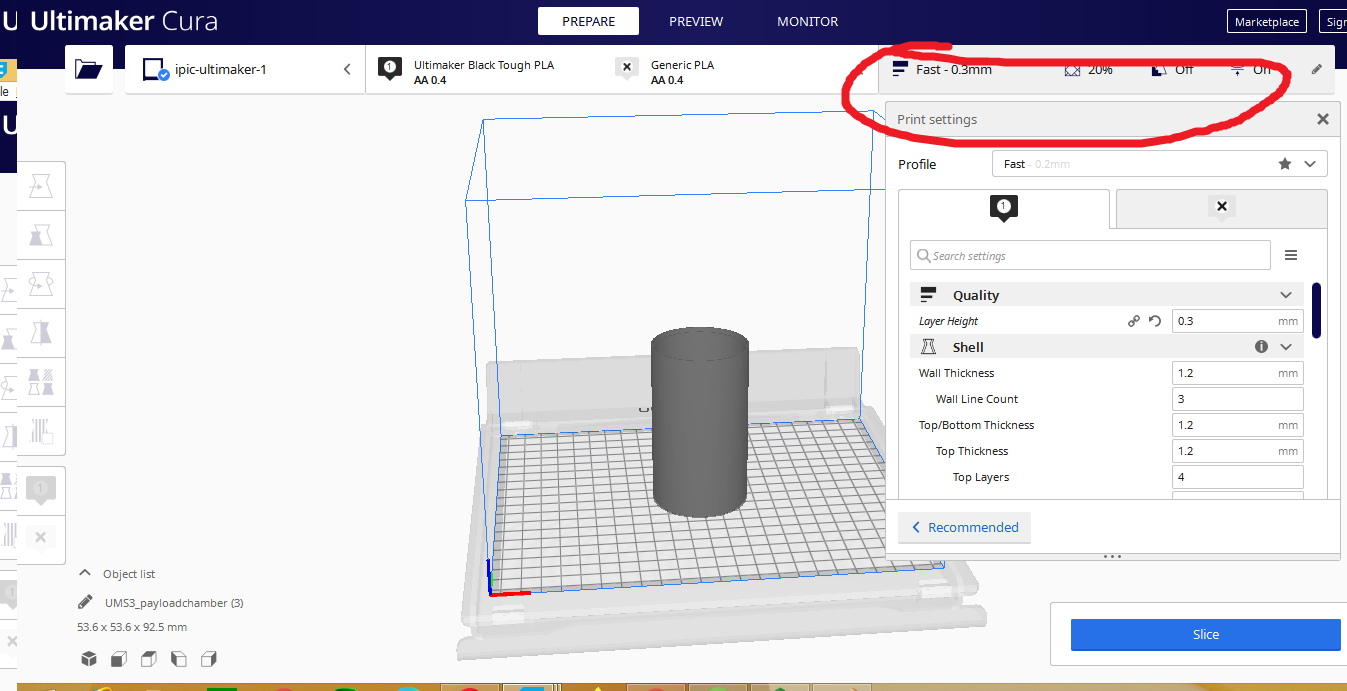
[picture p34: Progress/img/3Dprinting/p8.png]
[](img/3Dprinting/p8.png)

### 9. Change it to normal

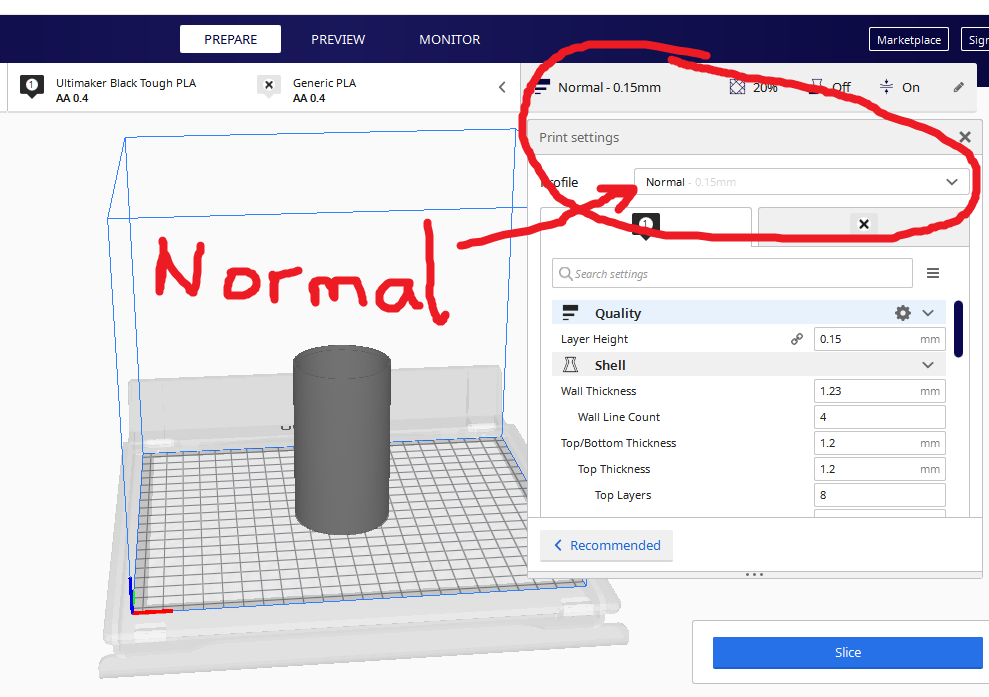
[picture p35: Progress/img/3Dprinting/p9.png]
[](img/3Dprinting/p9.png)

### 10. Change the layer height to 0.2mm

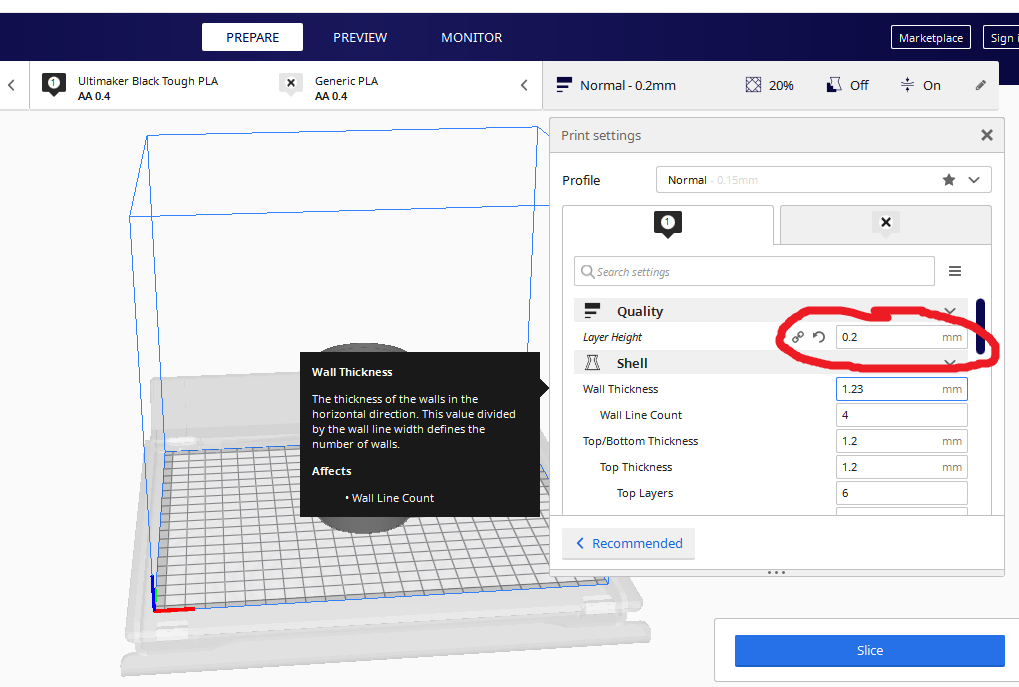
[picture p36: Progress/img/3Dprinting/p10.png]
[](img/3Dprinting/p10.png)

### 11. Maintain the top and bottom thickness to 1.2mm with 6 layers

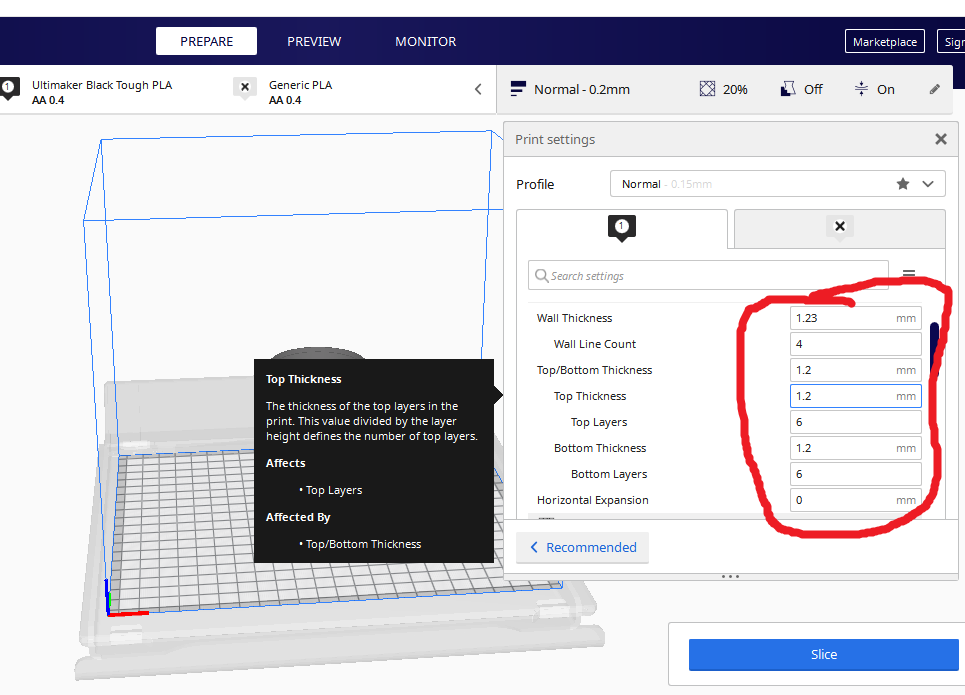
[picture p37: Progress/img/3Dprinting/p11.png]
[](img/3Dprinting/p11.png)

### 12. Change the infill pattern to `Lines` also the temperature set the printing temperature to `223 C` and build plate temperature to `70 C`

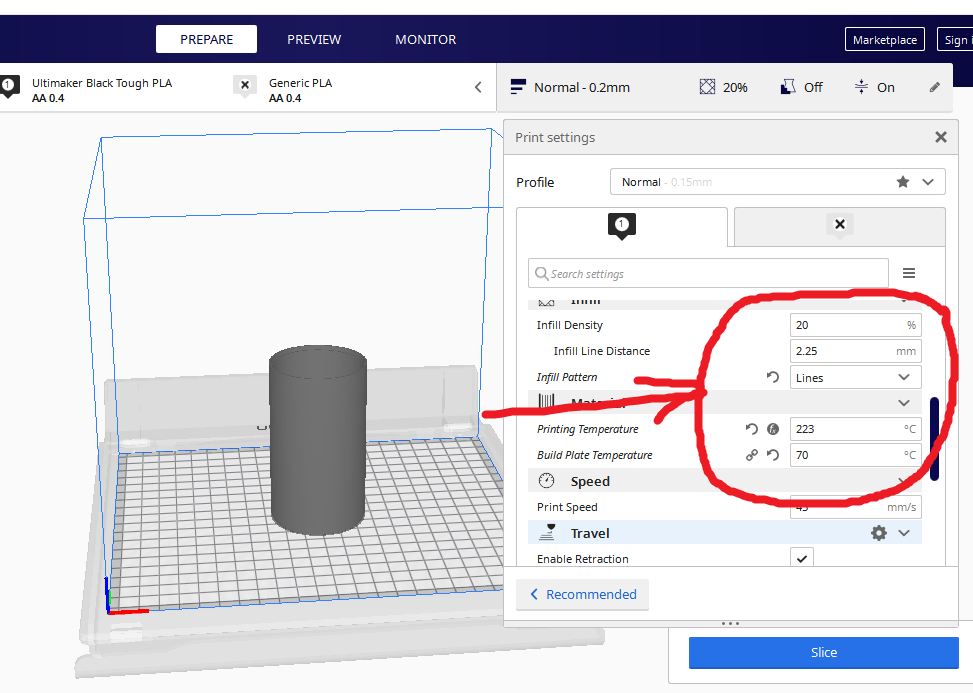
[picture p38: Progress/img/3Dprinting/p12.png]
[](img/3Dprinting/p12.png)

### 13. Enable print cooling at 100%

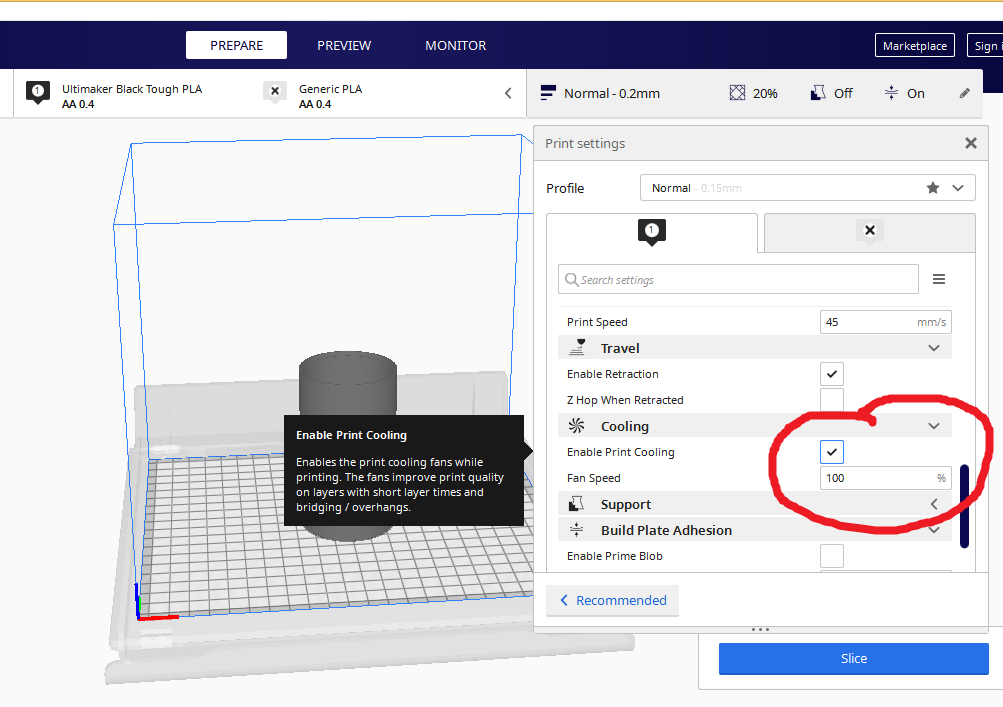
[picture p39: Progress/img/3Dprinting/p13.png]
[](img/3Dprinting/p13.png)

### 14. Change the build plate adhesion type to `Raft` with a margin of `5mm`

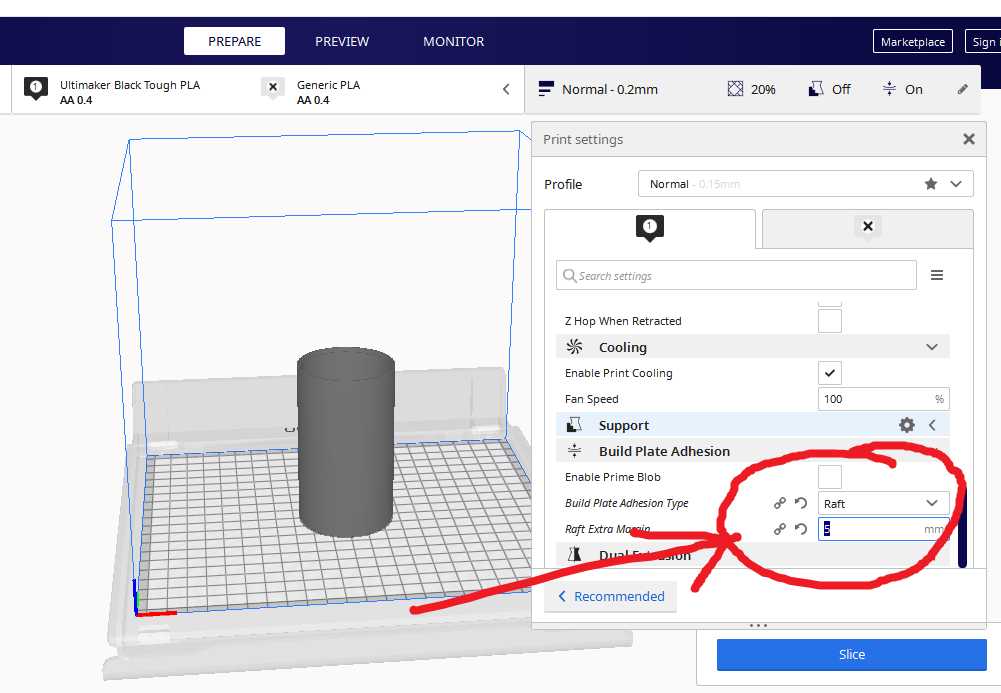
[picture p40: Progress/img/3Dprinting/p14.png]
[](img/3Dprinting/p14.png)

### 16. Click on the machine you want to print. This is for machines connected in the network and print

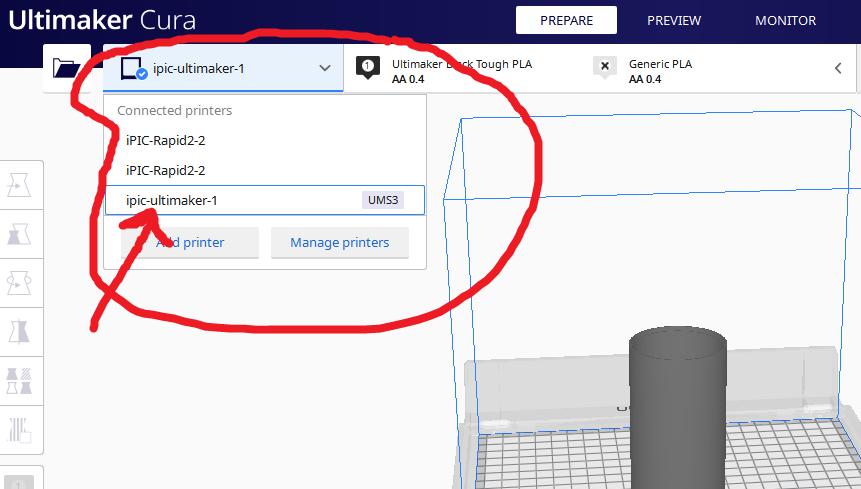
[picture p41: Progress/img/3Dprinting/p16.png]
[](img/3Dprinting/p16.png)

### 17. Monitor the prinitng process using a camera

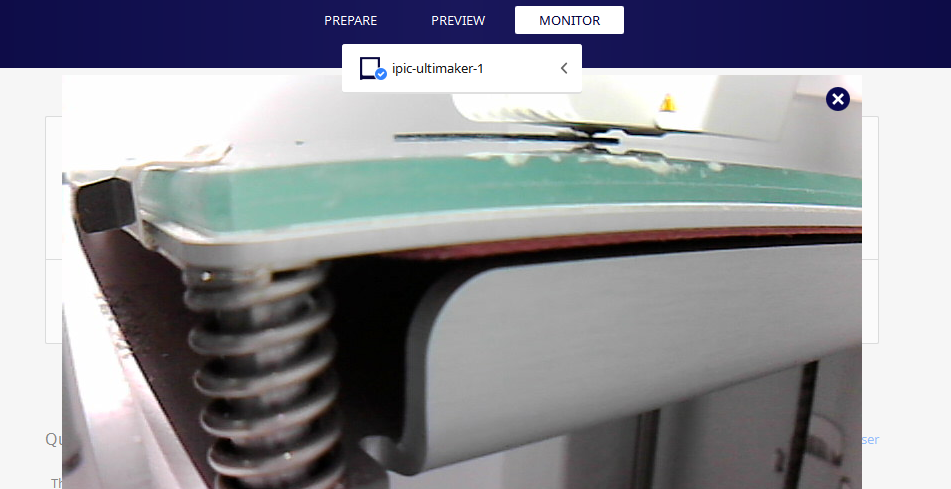
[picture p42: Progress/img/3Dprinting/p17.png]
[](img/3Dprinting/p17.png)

### 18. Monitor tab where you can find the progess

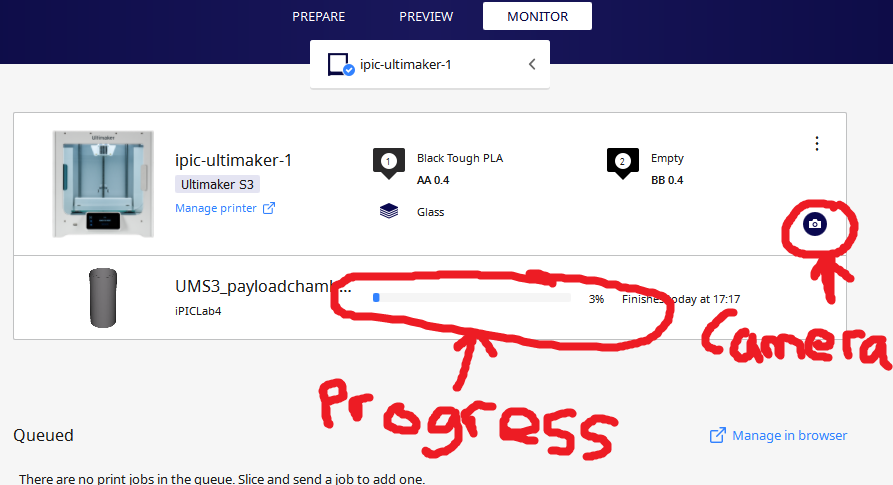
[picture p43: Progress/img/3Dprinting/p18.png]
[](img/3Dprinting/p18.png)

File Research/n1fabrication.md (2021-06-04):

# Design and fabrication of model rocket airframe using 3D printing 

## Abstract

In this paper, we describe the method to design and fabricate the airframe of the model rocket. Considering the lack of commercially available model rockets in Kenya, we designed and fabricated a low-cost model rocket using 3D printing. The airframe subsystem comprises a nose cone, body tube, fins, and parachute. For the material of the parachute, we chose nylon considering the lightweight and strength. The aerodynamic stability was confirmed by calculating the static margin using Openrocket software. 
We launched the developed model rocket and confirmed each subsystem worked properly. We believe this model rocket will be used for further development of the flight control system.

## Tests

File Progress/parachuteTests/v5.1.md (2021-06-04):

# Version 1.1

## Introduction

On this nose cone design we inserted a pin on the top part need the nose. This is to hold the nose part while the servo pushes it in from the bottom. We then added the spring mechanism to the base part this was to create an outward force to push the parachute out. This was done while maintaining the previous specs. The design can be found [here](https://github.com/nakujaproject/airframev1/tree/8eca6001235c1c59b9d69e9f7931666770087936)

### Some images

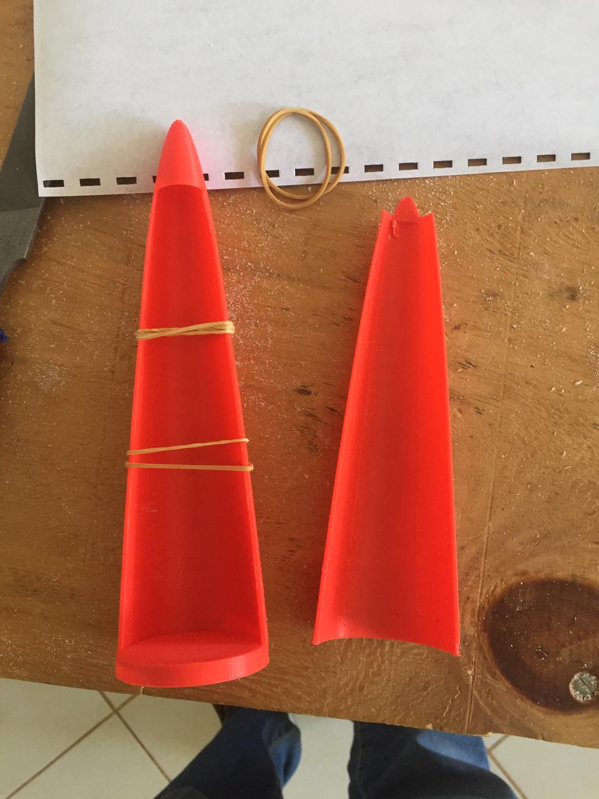
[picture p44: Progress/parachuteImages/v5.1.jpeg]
Nose cone image v5.1


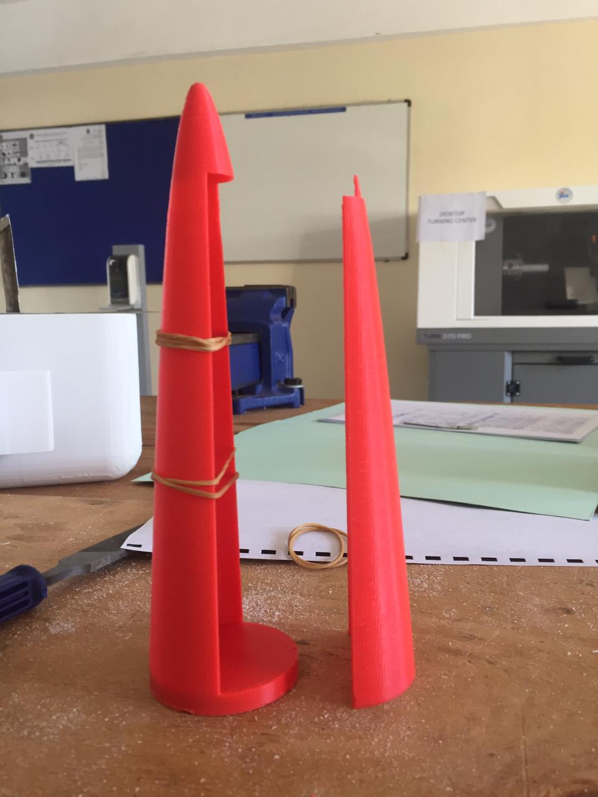
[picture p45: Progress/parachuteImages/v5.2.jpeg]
Nose cone image v5.2


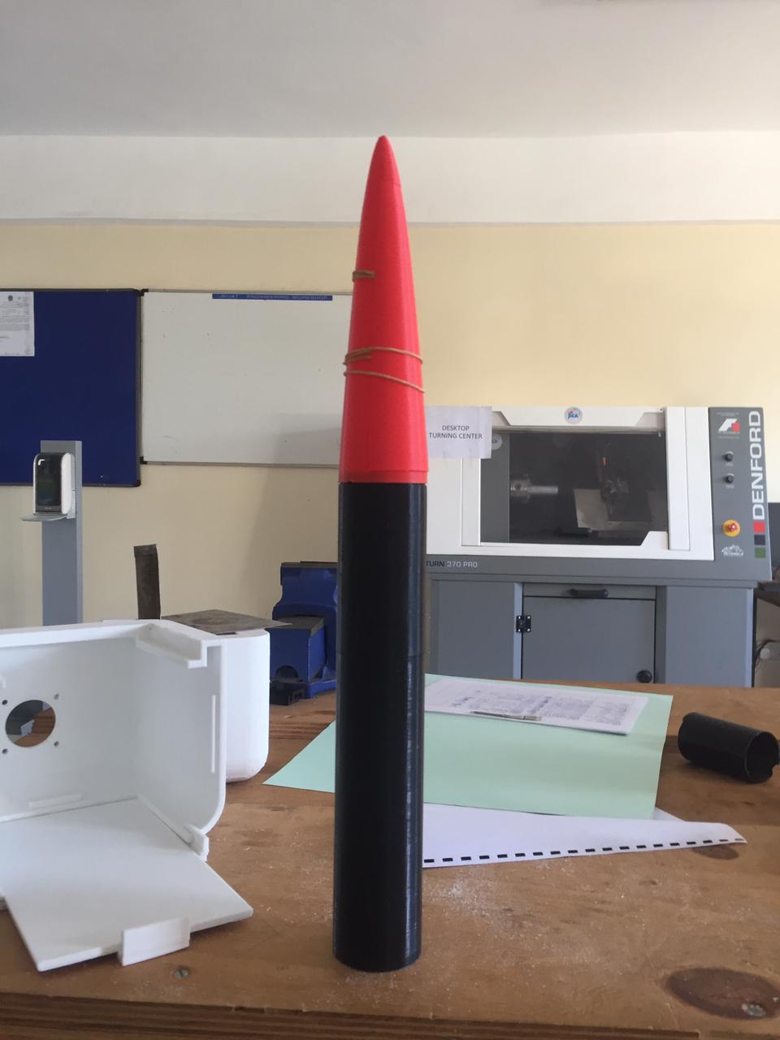
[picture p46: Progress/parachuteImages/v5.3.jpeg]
Nose cone image v5.3


## Problem

No problem so far awaiting testing

## Modifications

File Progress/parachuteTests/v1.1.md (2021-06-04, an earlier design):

# Version 1.1

## Introduction

This was pur first nose cone design for the rocket. We didn't have any prior know how on how the parachute ejection mechanism would work. The design files can be found [here](https://github.com/nakujaproject/airframev1/blob/e236fa8ae708f634feae82047ced389b07deac66/Design/nose-basepart1.stl)

### Some images

Nose cone image v1.1

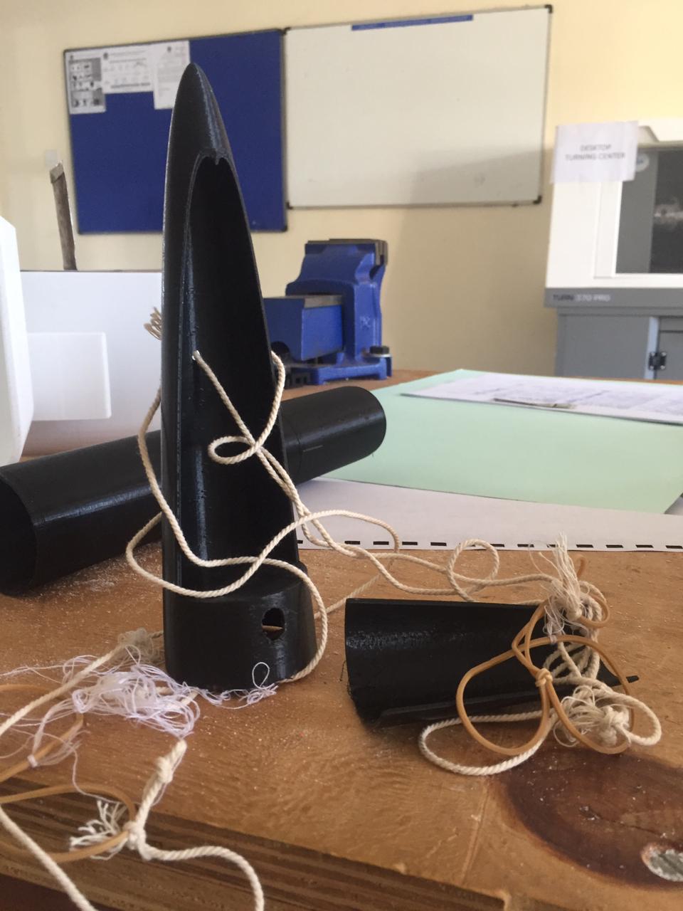
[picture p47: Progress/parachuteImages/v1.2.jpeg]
Nose cone image v1.2


## Problem

The parachute was not able to open up since the walls of the base part of the nose cone constrained it from ejecting.

## Modifications

We tried and make the opposite. So that the base part that joins with the rocket has less material while the cover covers all of it.

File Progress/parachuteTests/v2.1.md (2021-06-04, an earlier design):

# Version 2

## Introduction

This was our second nose cone design for the rocket. We tried and make the opposite. So that the base part that joins with the rocket has less material while the cover covers all of it. The servo mechanism remained the same to be able to hold the cover before opening it up. The design can be found [here](https://github.com/nakujaproject/airframev1/tree/cf36e4de9e948d365fbf606aeacae3a5e0503ae5)

### Some images

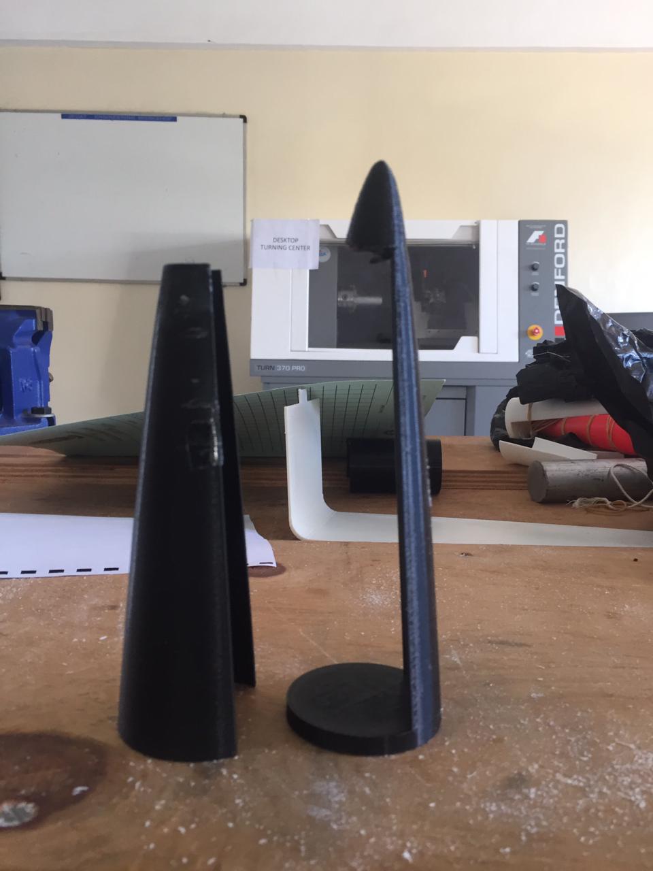
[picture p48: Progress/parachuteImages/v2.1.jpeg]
Nose cone image v2.1


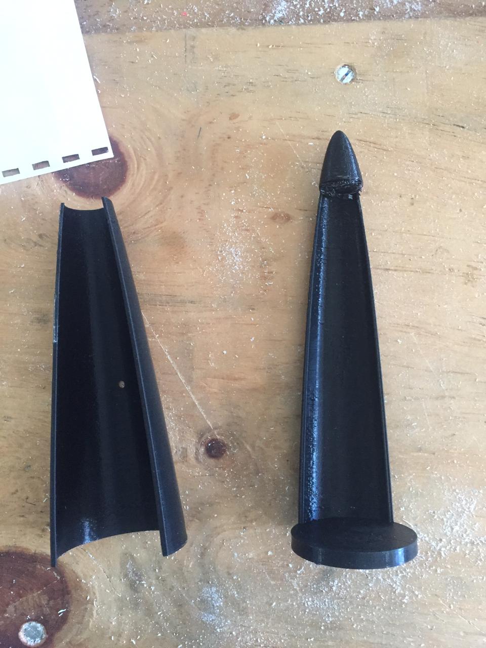
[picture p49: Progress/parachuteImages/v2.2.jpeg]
Nose cone image v2.2


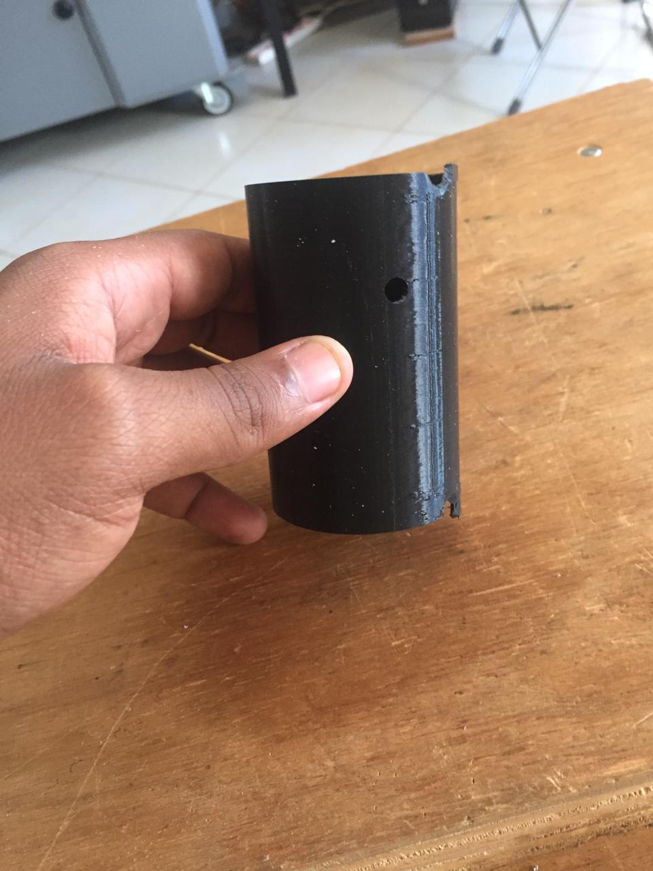
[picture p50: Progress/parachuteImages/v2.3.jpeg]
Nose cone image v2.3


## Problem

The servo arm was able to release the cover of the nose cone outside but the parachute still had trouble in deploying. Parachute was holding on to the cover this time instead of releasing.

## Modifications

We tried and made the cover to have 60% and the base have 40% of the total material coverage so that the parachute could have and easier time releasing. We also added the servo mechanism inside, so that it could push out the top part.

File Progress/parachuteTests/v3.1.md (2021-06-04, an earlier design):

# Version 3.1

## Introduction

This was our third nose cone design for the rocket. We tried and redesign the latch mechanism so that the servo arm could push the cover outside rather that the servo arm holding the cover inside before launch. The design can be found [here](https://github.com/nakujaproject/airframev1/tree/cf36e4de9e948d365fbf606aeacae3a5e0503ae5)

### Some images

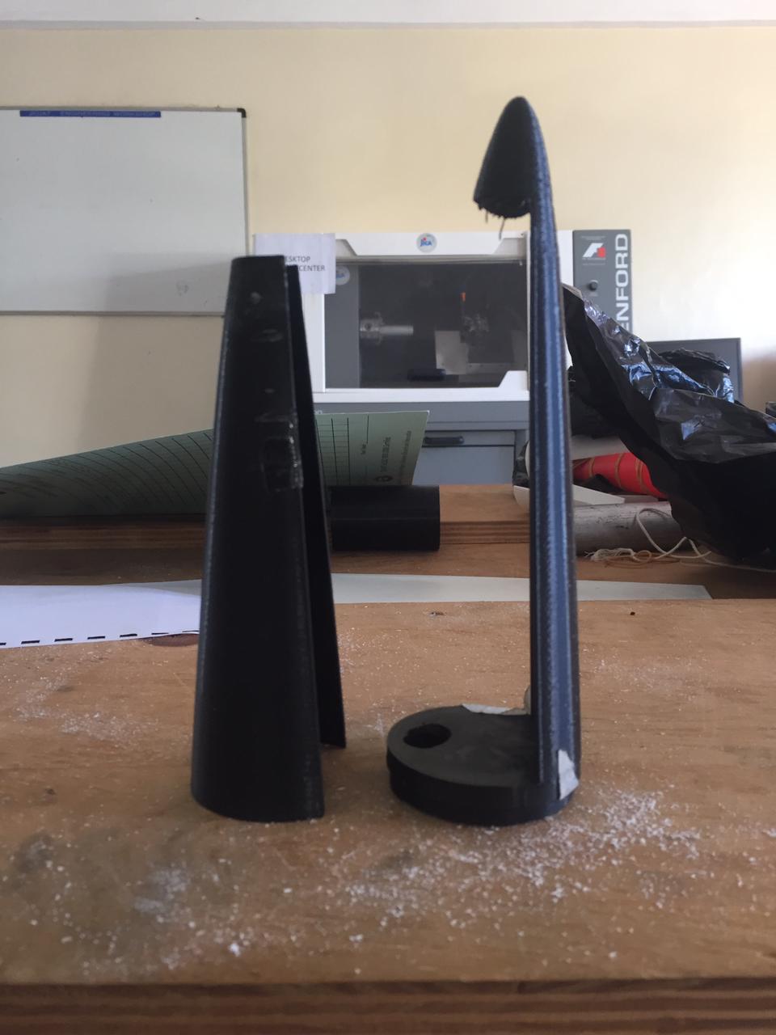
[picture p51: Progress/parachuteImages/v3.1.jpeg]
Nose cone image v3.1


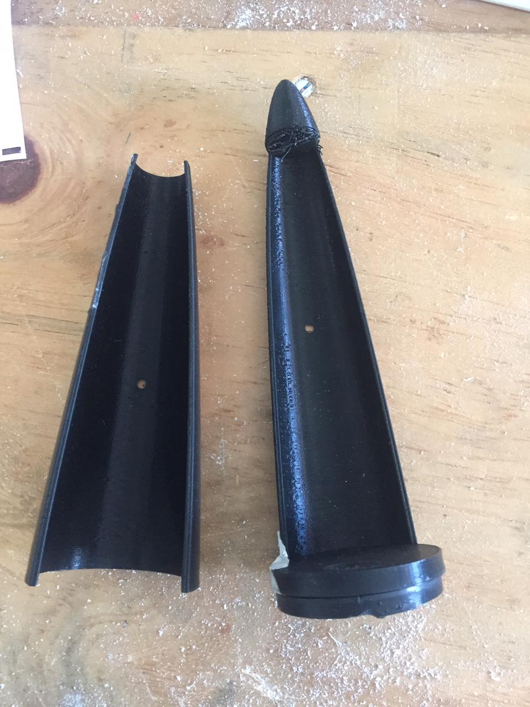
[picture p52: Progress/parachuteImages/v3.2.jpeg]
Nose cone image v3.2


Nose cone test v4.1

<!-- blank line -->
<figure class="video_container">
  <video controls="true" allowfullscreen="true">
    <source src="../parachuteImages/v3.1.mp4" type="video/mp4"></source>
  </video>
</figure>
<!-- blank line -->

## Problem

The servo arm was able to push the cover of the nose cone outside but the parachute still had trouble in deploying

## Modifications

We tried and make the opposite. So that the base part that joins with the rocket has less material while the cover covers all of it.

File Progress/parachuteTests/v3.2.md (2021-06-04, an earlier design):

# Version 3.2

## Introduction

On this nose cone design we tried and have it half-and-half so that the base part could cover half and also the cover to cover half. This was in order to make sure the parachute doesn't attach itself to the base part. We also added our first electronics chamber for the rocket. This is the chamber that houses the electronics bay which holds the electronic components. The servo mechanism was to shift from the nose to the electronics chamber. The design can be found [here](https://github.com/nakujaproject/airframev1/blob/8eca6001235c1c59b9d69e9f7931666770087936/Design/nose-basepart1.stl)

### Some images

Nose cone image v3.2

## Problem

The parachute maintained to attach itself on the top part rather than the base part. This make the ejection difficult since the parachute couldn't eject freely. When we were drilling we started off with a larger drill bit to drill the whole hole at once. The forces on the cutting edge corner were to high hence the electronics chamber weakened on the additive layers of 3D printing.

## Modifications

Trying to add spring mechanisms to the top part which covers the base part. This is to create an outward force which pushed the parachute out. We tried the next test starting of with smaller drill bits and gradually increasing the drill bit by a deviation of 1mm. We succeed in drilling through and mounting the servo motor.

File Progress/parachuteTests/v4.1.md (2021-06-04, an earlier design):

# Version 1.1

## Introduction

On this nose cone design we tried and have to change the dimensions rather than having it half-and-half so that the base part could cover half and also the cover to cover half, we had the base part to be at 70% and the top part at 30% of the coverage. We then added the spring mechanism to the base part this was to create an outward force to push the parachute out. The design can be found [here](https://github.com/nakujaproject/airframev1/tree/601282b1a38ceb6b29486d730ce19b3bf3055e32)

### Some images

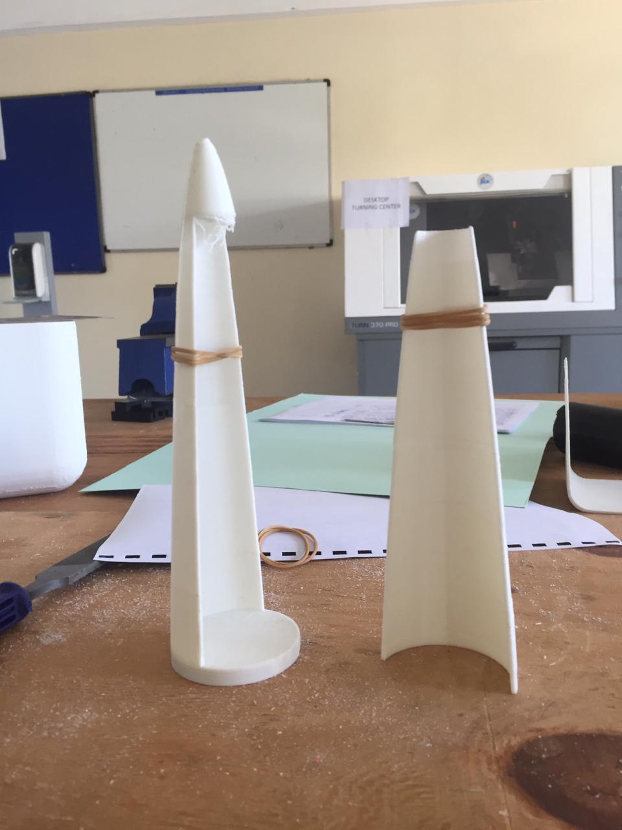
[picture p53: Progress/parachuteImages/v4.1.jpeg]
Nose cone image v4.1


Nose cone test v4.1

<!-- blank line -->
<figure class="video_container">
  <video controls="true" allowfullscreen="true">
    <source src="../parachuteImages/v4.1.mp4" type="video/mp4"></source>
  </video>
</figure>
<!-- blank line -->

## Problem

We didn't find a mechanism to hold the top part to the base part. So the cover was not holding the parachute in and could fly off any time possible.

## Modifications

We inserted a pin on the top part need the nose. This is to hold the nose part while the servo pushes it in from the bottom.

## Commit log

2022-03-14 Add cad files
    [N-2 rocket assembly1.iam, N-2 rocket assembly2.iam, body tube n-2.ipt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]
2022-03-15 This is the CAD design that is being used for the simulation
    [Rocket v6.step]
2022-07-06 Simulation with 300mm motor
2022-07-06 Simulation with 200 mm motor
2022-10-07 Add Propulsion CAD data
    [Assembly.iam, Assembly.stp, bulkhead.0001.ipt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]
2022-10-11 f(flight-control) add mounting bays, pcb and assembly
    [Assembly1.iam, OBJ_PCB_PCB_Flight control computer.ipt, OBJ_PCB_flight-control_2.ipt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]
2022-10-12 Avionics CAD files
    [PCB_PCB_N2-final launch PCB1_2022-10-12 (9).iam, battery holder.ipt, case v0.ipt]
